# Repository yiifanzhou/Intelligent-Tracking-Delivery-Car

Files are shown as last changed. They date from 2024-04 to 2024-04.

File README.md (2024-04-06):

# Intelligent Tracking Delivery Car
This is a course design from Design &amp; Bulid Ⅰ(First Semester).  

<p align="center">
摘要
</p>  

&emsp;&emsp;为增加和改进现有轮式机器人功能，并为物流运输业提供更加智能化的选择，项目组致力于研发一种基于Arduino系统的能够自动循迹并精确投放的智能派送车。  

&emsp;&emsp;项目开发初期，通过资料收集、问卷调查、项目规划五步法、产品概念生成和选择的一般方法等研究方法，确定零件功能和市场需求、建立目标产品规格、分析并选择产品概念。中期，使用Solid works对零件进行三维建模以及组装；设计控制系统接线图和控制流程图；采用Arduino编程进行算法的设计和调试。后期，利用激光切割技术处理底板，采用3D打印技术打印投放装置，完成智能派送车实体模型的建立。

&emsp;&emsp;设计出的智能派送车能够自动沿黑线行进，并在多个投递处准确投放包裹，完成循迹与投放任务。

&emsp;&emsp;接下来是一些项目图片展示：  

</p>  

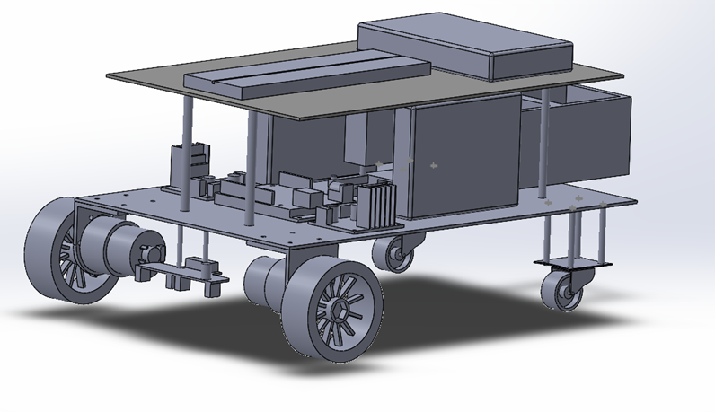
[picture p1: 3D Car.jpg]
  

<p align="center">
图1 整车设计图
</p>  

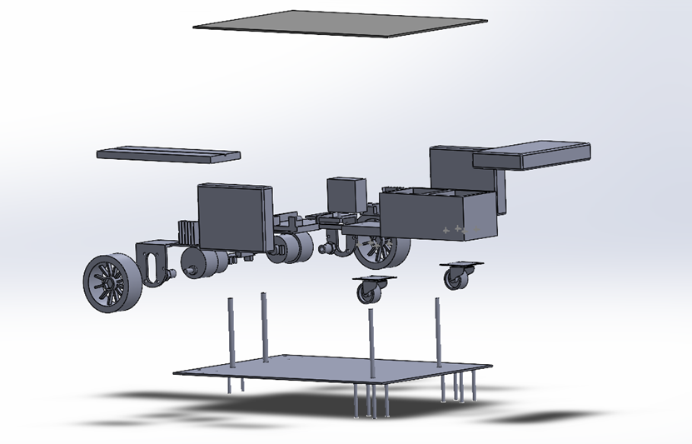
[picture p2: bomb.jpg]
   

<p align="center">
图2 整车爆炸图
</p>  

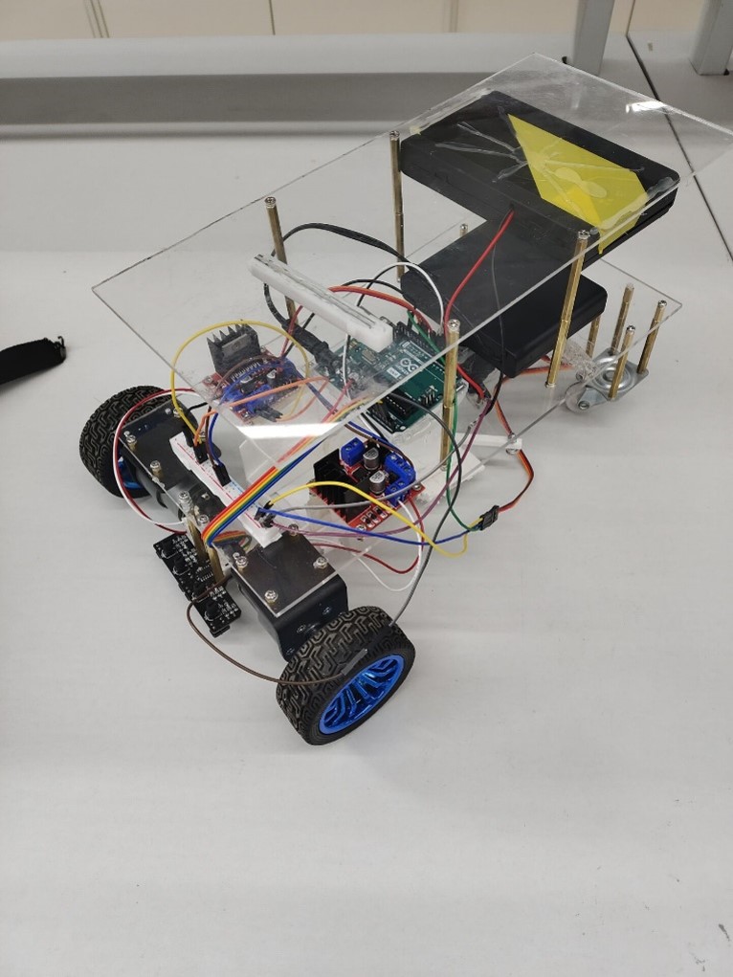
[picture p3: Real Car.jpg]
  

<p align="center">
图3 实物演示图
</p>

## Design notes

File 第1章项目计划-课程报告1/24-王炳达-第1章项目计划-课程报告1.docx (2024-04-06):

# 课程报告1 项目计划

## 1.1 项目相关资料综述

### 1.1.1 前言

随着科技的发展，智能派送车在各个领域都有广泛的应用前景，它可以代替人类完成恶劣环境下的货物搬运、设备检测等任务[1]。智能派送车是轮式移动机器人研究领域的一项重要内容，涵盖了机械、汽车电子、电气、计算机、检测技术、模式识别与智能控制等多个学科。它是陆地自主行驶车辆 (Autonomous Ground Vehicle) 的一种。AGV在社会生活的各个领域都有着非常广阔的应用前景。在西方发达国家，移动式自主服务机器人已广泛应用于医疗福利服务、商场超市服务、家庭服务等领域；AGV在军事领域也有着重要的应用价值， 美国军方把部分机器人技术视为未来战斗系统 (Future Combat System) 的重要组成部分[2]。本文基于基础的智能派送车展开资料查阅，对此进行研究。

### 1.1.2 智能小车的国内外研究现状

在国外，有关移动机器人的研究相对比较成熟。原因有二：一是研究起步早，二是投入经费多。上世纪50年代初，国外就开始对人工智能、机器人视觉、自动导航等技术进行理论层面的研究。进入上世纪90年代，移动机器人开拓各个应用领域，美国“火星探路者”、火星漫游车“索杰纳”、“勇气”号、“机遇”号相继进行探索，并完成科学探测任务。

在国内，对移动机器人的研究起步晚，研究的突破性进展比较少。国内最早从事智能汽车和智能交通研究的是清华大学，研究方向集中在汽车导航、车载微机、自主避障、行驶安全等方面。近年来，各个高校重点开展了移动机器人相关的研究，并获得一定成绩，如上海交通大学研制的高性能自主移动机器人Frontier-ITM，获得过国家863高技术计划专项支持。

### 1.1.3 项目产品组成

（1）直流减速电动机

直流减速电机是在直流电机（马达）的基础上配备了齿轮减速箱，从而能够提供较低的转速，及较大的力矩。其精度高、体积小、噪音低、耐用、耗能低、安装方便，适合本项目中对智能派送车的传动。

（2）传感器系统

传感器是一种检测装置，能感受到被测量的信息，并能将感受到的信息，按一定规律变换成为电信号或其他所需形式的信息输出，以满足信息的传输、处理、存储、显示、记录和控制等要求[3]。

项目组使用的是光学（红外）传感器，红外发射管不断发出红光，由于路线中地面与轨迹的颜色差异，使得接受管接收到的光强也有差异进，进而由转换元件输出特定的电流或电压信号，从而实现智能派送车的循迹功能。

（3）Arduino编程

Arduino并不仅仅是一块小小的电路板，还是一个开放的电子开发平台。它既包含了硬件——电路板，也包含了软件——开发环境和许许多多开发者、使用者创造的代码、程序。Arduino抛开了传统硬件开发的复杂操作，不需要了解硬件的内部结构和寄存器设置，也不需要过多的电子知识和编程知识，而只需通过简单的学习，了解各个引脚和函数的作用，便可利用它开发出各种出色的项目。

Arduino它的优势十分明显：一是跨平台，Arduino IDE可以在Windows、Mac OS X和Linux三大主流操作系统上运行，而其他的大多数控制器只能在Windows上开发；二是简单清晰的开发，Arduino IDE基于Processing IDE开发，这对于初学者来说极易掌握，同时又有着足够的灵活性，Arduino 语言是基于Wiring语言开发的，是对AVRGCC库的二次封装，并不需要太多的单片机基础和编程基础，只要简单地学习后就可以快速地进行开发；三是开放性，Arduino的硬件原理图、电路图、IDE软件及核心库文件都是开源的，在开源协议范围内可以任意修改原始设计及相应代码；四是从硬件开发趋势来说，Arduino不仅仅是全球最流行的开源硬件，也是一个优秀的硬件开发平台，更是硬件开发的趋势。

Arduino 简单的开发方式使得开发者更关注于创意与实现，可以更快地完成自己的项目开发，大大节约学习的成本，缩短开发的周期。鉴于Arduino的种种优势，越来越多的专业硬件开发者已经或开始使用Arduino来开发项目和产品；越来越多的软件开发者使用Arduino进人硬件、物联网等开发领域；在大学里，自动化、软件专业，甚至艺术专业，也纷纷开设了Arduino相关课程[4]。

（4）Solid works建模

Solid works是项目组在项目中对工件建模所采用的技术。Solid works软件功能强大，组件繁多，操作简单方便、易学易用。Solid works资源管理器是同Windows资源管理器一样的CAD文件管理器，用它可以方便地管理CAD文件。在强大的设计功能和易学易用的操作（包括Windows风格的拖/放、点/击、剪切/粘贴）协同下，项目组能在比较短的时间内完成更多智能派送车工件的设计，并更快地将高质量的产品投入后续打印工序。

（5）3D打印技术

3D打印技术即快速成型技术的一种，是一种以数字模型文件为基础，运用粉末状金属或塑料等可粘合材料，通过逐层打印的方式来构造物体的技术。项目中所使用的打印材料应具有较好的硬度、强度，以及一定的尺寸稳定性、耐磨性，且便于成型加工与机械加工。从而制作出较好的组件，继而进行组装工作。

## 1.2 项目管理

### 1.2.1 项目组成员

组长：王炳达；

组员：王宗辉、刘洋、周艺梵、郭法。

### 1.2.2 项目分工图

对智能派送车的各个模块进行划分，再分配给每位组员。工作分解结构图如图1-1所示。

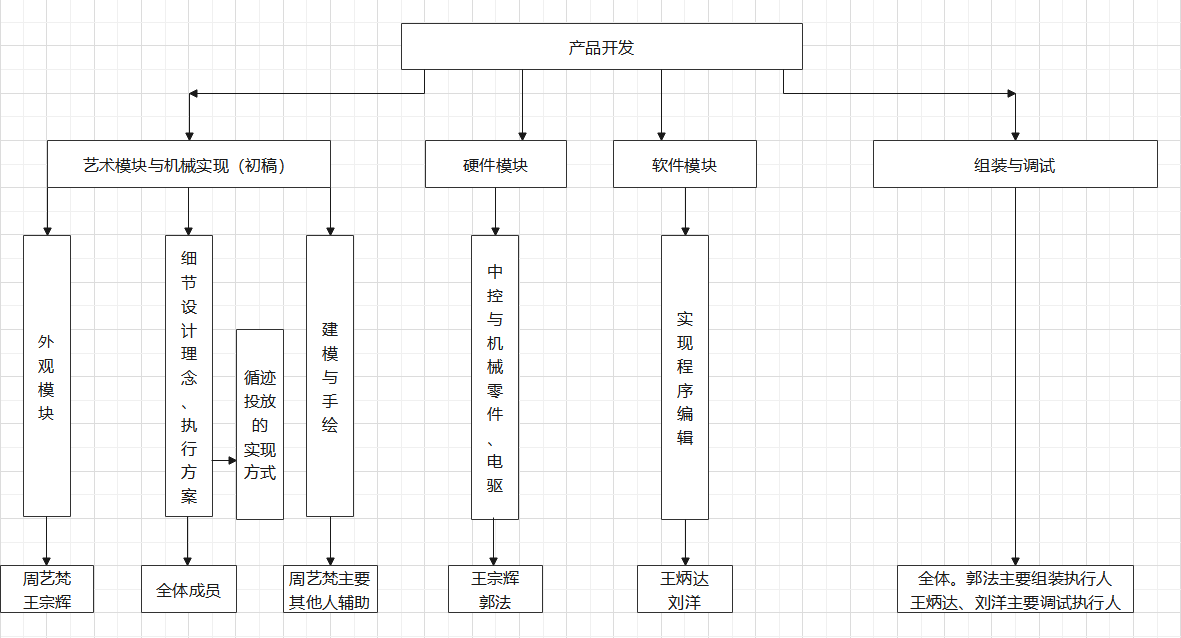
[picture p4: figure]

图1-1 工作分解结构图

### 1.2.3 进度安排甘特图

根据工作分解安排工作进度，进度安排甘特图如图1-2所示。

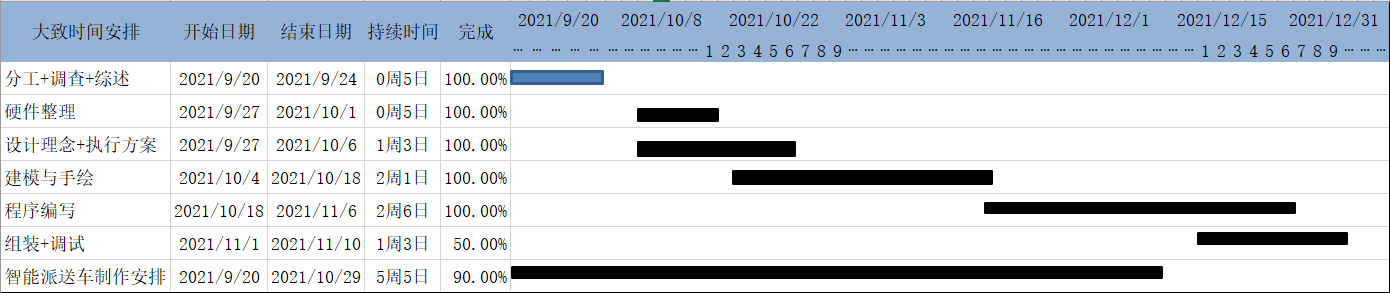
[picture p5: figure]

图1-2 进度安排甘特图

## 1.3 工程师职责

世界工程组织联盟提出了工程师伦理责任准则大致包括以下内容：

（1）应维护大众之安全、健康和福祉，以加强安全和环境的保护为最高指导原则。

（2）对技术后果负有责任，并且要告知公众技术可能的结果。

（3）严守业务机密，避免利益冲突。

（4）承办工程业务应以自己的专业领域提出服务与建议，态度应谨慎、认真。

（5）对待各方应持有公平、有礼、善意的态度，对雇主否决或忽视的重要工程的决策，应将可能发生的后果据理说明。

（6）吸收新的知识以加强专业能力。

（7）对他人违法或者有失伦理道德的一切工程技术上的决定或行为适时揭发。

根据上述条例对工程师不同层面的要求，现将其进行分类，如图1-3所示。

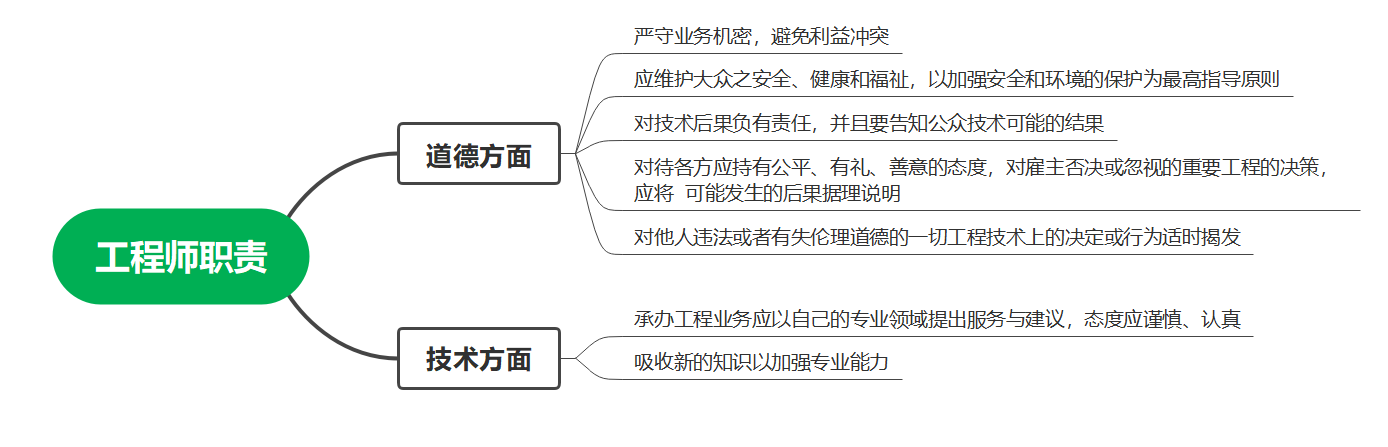
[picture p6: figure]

图1-3 工程师职责图

## 1.4 任务完成情况小结

在第5周至第8周期间，项目组对智能派送车的发展历程，现阶段所面临的一些问题以及应用前景进行初步的了解，并制定较为详细的制作计划。王炳达组织进行小组分工，并完成进度安排甘特图以及团队日历的制作；刘洋完成对工程师的职责的查找和分类；周艺梵完成课程报告PPT的制作；王宗辉完成项目相关资料的综述；郭法完成会议记录。

## 1.5 小组会议记录

“设计与建造”课程小组会议记录

议题 | “智能派送车”的初步规划与任务分工
组长 | 王炳达 | 年级/班级/组别 | | 2021级二班第4组
组员 | 郭法、周艺梵、王宗辉、刘洋
会议时间 | 2021年9月14日 19：00-21：00 | | 会议地点 | 郑东图书馆205读者研究厢
讨论内容 | 1．产品开发任务模块，进度。分为硬件，软件和组装等模块。 2．成员分工，工作分解。软件模块由王炳达负责；外观模块由周艺梵负责；细节设计理念由全体成员负责；建模与手绘主要由周艺梵负责；组装和调试主要由郭法负责。 3．PPT、文献综述、查阅资料的安排。PPT主要由周艺梵负责；文献综述由王宗辉和周艺梵负责；查阅资料硬件系统和结构模块由王宗辉负责，软件模块由周艺梵负责，工程师职责由刘洋负责。 4．各成员的相关问题和解决方案。讨论职责的细分和需要的资料和软件等事宜，都一一解决。 5．甘特图和日历的相关问题。规划将来任务并由王炳达做处理制作和完善。 6．PPT展示分工。王炳达负责讲分工和时间安排；王宗辉等三人负责讲相关资料；郭法负责讲会议记录。 7．智能派送车构造和软件使用相关情况。讨论关于智能派送车构件和材料，统一solid works的安装等事宜。
下一步工作计划 | 1．查阅资料以及个人综述，在各成员完成任务后。 2．讨论课程报告与PPT制作，在制作完成后统一讨论。 3．进一步讨论智能派送车的构造与硬件，在课程报告和PPT完成后。 4．讨论软件相关问题，下一次会议时间。
附件材料清单 | 无

参会成员：王炳达 刘洋 郭法 王宗辉 周艺梵

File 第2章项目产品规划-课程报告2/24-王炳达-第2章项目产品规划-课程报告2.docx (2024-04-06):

# 课程报告2 项目产品规划

## 2.1 项目产品规划

### 2.1.1 产品功能

项目组结合无人驾驶和无人派送货物的时代热点，在智能方面深度挖掘和深刻研究，设计出的智能派送车具备无人驾驶、自主自动循迹、定点准确投放包裹的功能，能够广泛应用于市场，充分满足人们需求，为智能派送这一方向提供建设性思路。

### 2.1.2 产品规划

（1）识别机会

在当今时代，网购等商业活动十分发达，但在这样一个智能化的时代，项目组发现重复性体力劳动给生活带来许多不便。经过讨论认为，智能派送车的出现，能够帮助人们减少体力劳动，具有广阔的潜在市场。同时，这样的产品也具有可行性，通过传感器系统、软件系统、硬件系统等各个系统的协同工作，达到智能派送的效果，同时也能够不断地迭代更新，升级产品。该产品具有较强的实用性，具有较好的获取市场份额的能力。通过项目组的不断分工和完善，该产品也能够具有较强竞争优势。更为关键的是，该产品投入成本小，风险小，值得尝试。

（2）评估并确定项目的优先级

项目组确保以客户为中心，确保满足客户的需求。同时，项目组也应当不断探索新的技术，争取在软硬件方面能够实现技术突破，实现技术方面的领先。

（3）分配资源和计划时间

任务分配和时间安排具体如上文中图1-1和1-2所示。

（4）完成项目前期规划

1）关键商业目标

① 支持小组战略目标：制作高效智能派送车。

② 产品推出时间：2022年1月14日前。

2）获益提议

① 产品性价比相对较高。

② 产品安全，不容易产生安全方面的问题。

③ 产品功能比较实用，节省人力。

3）主要市场

快递投放领域（公司为主）。

4）假设和约束

假设：

① 利用Solid works软件制图，进行建模与手绘。

② 掌握Arduino的编程知识。

③ 掌握中控与机械零件、电机驱动模块。

④ 实现组装和调试。

约束：

① 时间方面：可能会出现时间分配不当，进度缓慢的情况，项目组应按照甘特图进行适当改变。

② 经费方面：经费有限，需要合理利用各种分配的材料，做到效率最大化。

③ 能力方面：第一次接触软硬件知识，项目组应该努力学习相关方面的知识。

为更加直观地明确假设和约束内容，将假设和约束制成图表形式如下图2-1所示。

假设和约束
假设
利用Solid works进行制图，进行建模与手绘
掌握Arduino及其编程知识
约束
能力方面
掌握中控与机械零件、电机驱动模块
实现组装和调试
时间方面
经费方面

图2-1 假设和约束概念表

5）利益相关者

① 产品开发者：产品开发者通过制作开发掌握知识并学习技能。

② 产品使用者（个体）：减少不必要体力劳动，能够提高工作效率。

③ 快递公司：减少人力成本和财力成本，提高快递公司的利润。

④ 快递员：影响快递员的工作，在一定程度上减少快递员数量。

（5）反思过程和结果

1）经过项目组讨论，前期时间安排等工作存在不妥，项目组将灵活变更和调整完成产品的时间。

2）项目组未考虑使用创新的软硬件，应在这方面不断调整。

3）开发团队在时间管理方面存在部分问题，应提高工作效率。

## 2.2 客户需求调研

### 2.2.1 客户需求分析过程

（1）步骤一：收集来自客户的原始数据

通过调查问卷得到的客户需求数据如表2-1所示。

表2-1 智能派送车客户需求数据（客户调查表）

问题 | 客户需求 | 需求解释
智能派送车的安全性和可用性的评价与建议 | 如图2-2所示。 | 客户普遍认为安全性是可靠的。
智能派送车的产业化需要考虑的问题 | 如图2-3所示。 | 客户普遍认为要考虑安全性、人性化、环境识别度、成本以及接受度问题。
智能派送车的大范围推广和使用存在的阻碍 | 如图2-4所示。 | 客户认为大众可能会有心理接受上的障碍以及对安全的担心和成本的担忧。
市场上正在使用的智能派送车的改进点 | 如图2-5所示。 | 智能派送车的智能性和灵活度有待提高。
关于智能派送车的其他建议 | 希望得到更快的普及。 | 客户对智能派送车的未来抱有很高的期待。

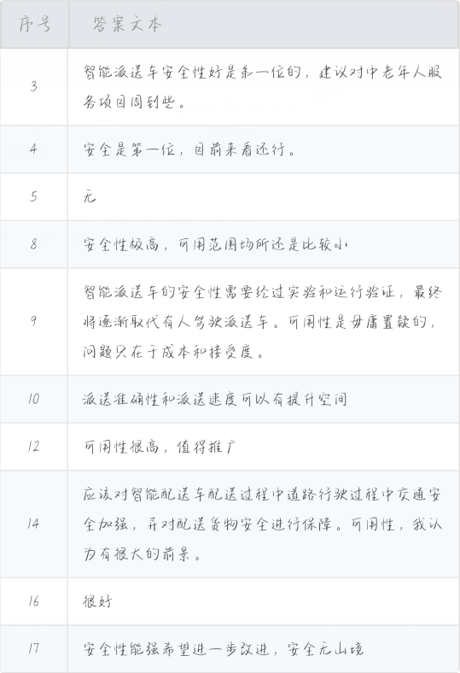
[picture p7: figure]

图2-2 智能派送车的安全性和可用性的评价与建议

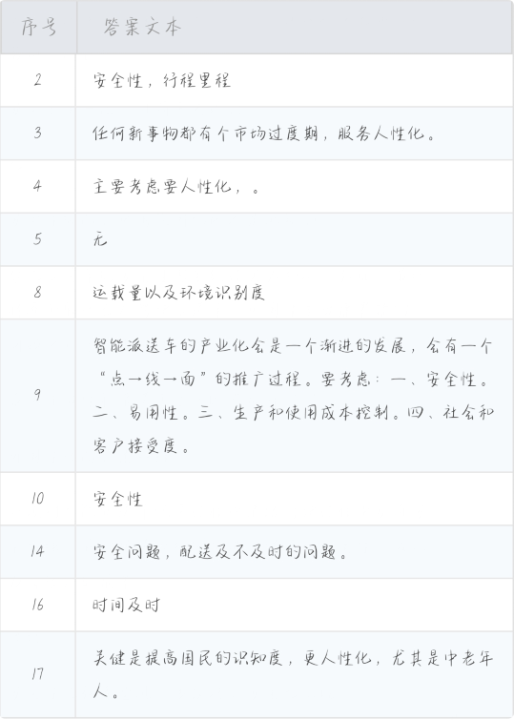
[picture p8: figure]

图2-3 智能派送车的产业化需要考虑的问题

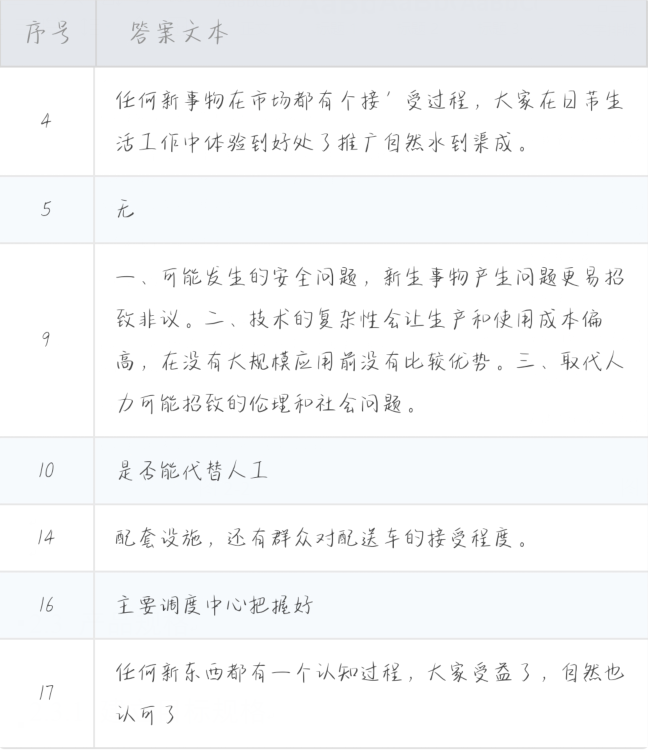
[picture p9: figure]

图2-4 智能派送车的大范围推广和使用存在的障碍

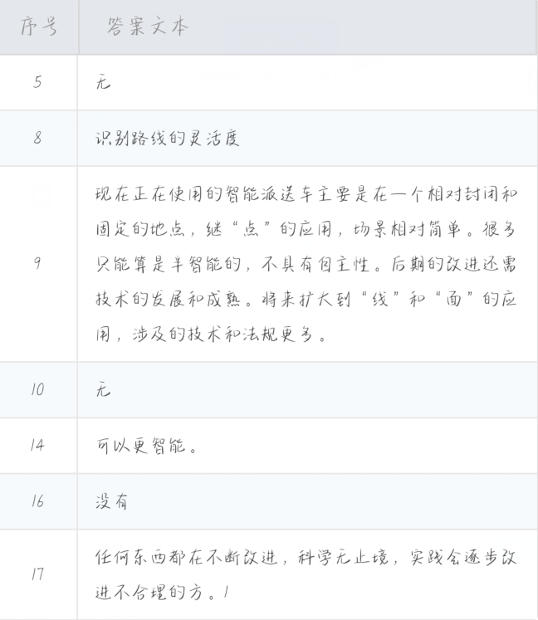
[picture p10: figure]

图2-5 市场上正在使用的智能派送车的改进点

（2）步骤二：根据客户需求解释原始数据

1）编写需求书的五个原则

① “做什么”而非“怎么做”。

② 产品特点。

③ 肯定而非否定。

④ 产品属性。

⑤ 避免“必须”和“应该”。

（3）步骤三：组织客户需求的层次结构

（4）步骤四：确定客户的需求的相对重要性

（5）步骤五：反思结果和过程

1）是否与目标市场上的主要顾客都进行了交流？

2）是否确定出已识别的最主要的需求？

3）是否捕捉到目标客户的潜在需求？

4）如何完善改进客户需求分析流程？

### 2.2.2 产品目标树

依据客户需求分级层次列表，可以绘制出产品目标树如图2-6所示，产品目标树显示客户需求的目标和子目标。

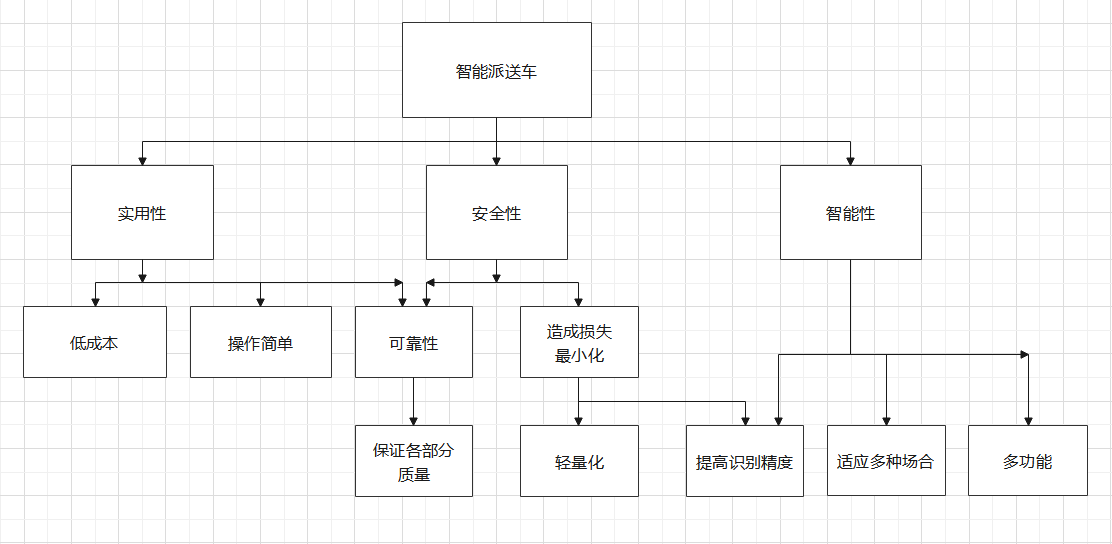
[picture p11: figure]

图2-6 产品目标树

## 2.3 产品规格

### 2.3.1 建立目标规格

（1）准备指标列表

为了在客户需求与度量指标之间建立联系，项目组需要了解用户的需求与智能派送车的性能，如表2-2所示。

表2-2 智能派送车需求列表

序号 | 需求
1 | 安全性
2 | 效率
3 | 派送费用
4 | 精准度

掌握所需指标可以准确设计出符合客户需求的智能派送车，智能派送车的指标列表如表2-3所示。

表2-3 智能派送车指标列表

序号 | 零件 | 单位 | 对应需求序号
1 | 车长 | mm | 1
2 | 车宽 | mm | 1
3 | 前轮直径 | mm | 2、4
4 | 转向轮直径 | mm | 4
5 | 物块大小 | mm*mm*mm | 2、3
6 | 物块存储器 | mm*mm*mm | 2、3
7 | 投放误差 | mm | 4
8 | 小车速度 | m/s | 2
9 | 电机电压 | V | 1、2
10 | 总价 | RMB | 3

（2）收集竞争产品的指标基准信息

通过调查资料了解竞争对手的详细规格信息，可以对项目组的智能派送车进行改进并更好满足客户的需求，竞争产品指标信息如表2-4所示。

表2-4 竞争产品指标信息

项目序号 | 项目 | 单位
1 | 前轮轮径、轮宽 | mm
2 | 转向轮轮径、轮宽 | mm
3 | 赛道测试时间 | s
4 | 传感器工作距离 | mm
5 | 车长、宽 | mm
6 | 电机电压 | V
7 | 小车车速 | m/s
8 | 总价 | RMB

（3）为每个指标设置理想值和临界可接受值

分析现有产品参数，为给定的产品指标设定目标值，包括理想值和临界可接受值，产品目标指标表如表2-5所示。

表2-5产品目标指标表

零件 | 目标值 | 理想值 | 临界可接受值
车长 | 250mm | 230-280mm | 200-300mm
车宽 | 150mm | 120-180mm | 100-200mm
前轮直径 | 60mm | 50-70mm | 40-70mm
转向轮直径 | 30mm | 25-35mm | 20-40mm
物块大小 | 50mm*50mm*50mm | 50mm*50mm*50mm
物块存储器 | 55mm*55mm*55mm | 60mm*60mm*60mm
投放误差 | 0 | 0-20mm | 0-40mm
电机电压 | 5V | 4.5-5.5V | 4-6V
总价 | 600RMB | 550-650RMB | 500-700RMB

（4）反思结果和过程

在确定产品指标中，项目组成员经过讨论与搜集资料，比对已有产品规格，衡量理想值，并为智能派送车做出合理临界值。

### 2.3.2 产品规格参数表

罗列材料清单，查询估计每一个组件的购买价格，初步预估产品成本。从成本角度进行估算能设计出更符合客户需求的产品，智能派送车的组件清单列表如表2-6所示。

表2-6 智能派送车的组件清单列表

组件名称 | 数量 | 参考单价/元
Arduino开发板 | 1套 | 150
面包板 | 2块 | 10
接插线 | 1套 | 20
电池盒 | 2个 | 10
直流减速电动机 | 2个 | 30
电动机驱动模块 | 2个 | 30
传感器模块 | 2个 | 50
3D打印材料 | 不限 | 350

### 2.3.3 需求——指标矩阵

使用需求指标矩阵可以更加明确地表示出客户需求与度量指标之间的联系，如表2-7所示。

表2-7 智能派送车的需求——指标矩阵

指标 需求 | | 1 | 2 | 3 | 4 | 5 | 6 | 7 | 8 | 9
| | 小车的宽度 | 优化软件功能 | 额定载重量 | 转弯半径 | 停位精度 | 投放精度 | 行驶速度 | 工作电压 | 传感器灵敏度
1 | 小车的安全性 | • | | | •
2 | 提高小车速度 | | | | | | | • | •
3 | 获知位置信息 | | | | | • | | | | •
4 | 保护用户隐私 | | • | | | | | | | •
5 | 降低派送费用 | | | •
6 | 提高额定载重量 | | | •
7 | 提升投放精准度 | | | | | | • | | | •
8 | 自动识路功能 | | | | | | | | | •

## 2.4 任务完成情况小结

在第9周至第11周期间，项目组对智能派送车的产品规划进行完善，面向社会大众进行客户需求调研，并制定较为详细的制作计划。王炳达对客户需求进行调查；刘洋完成产品的详细规划；周艺梵、郭法完成产品规格的明确；王宗辉对小组会议进行记录以及对任务完成情况进行总结。

## 2.5 小组会议记录

“设计与建造”课程小组会议记录

议题 | “智能循迹派送小车”的项目规划
组长 | 王炳达 | 年级/班级/组别 | | 2021级二班第4组
组员 | 郭法、周艺梵、王宗辉、刘洋
会议时间 | 2021年10月14日19：00-21：00 | | 会议地点 | 郑东图书馆406读者研究厢
讨论内容 | 1．项目规划包含产品规划五步骤和产品任务书。 2．成员分工，工作分解。客户需求调研由王炳达负责；PPT、产品规格由周艺梵、郭法负责；产品规划由刘洋负责；小组会议记录和任务完成小结有王宗辉负责。 3．各成员的相关问题和解决方案。讨论职责的细分和需要进行的问卷调查等事宜，都一一解决。 4．甘特图和日历的相关问题。规划将来任务并由王炳达做处理制作和完善。 5．小车规格应按照客户调查表明确目标、需求和指标。
下一步工作计划 | 1．在各成员完成任务后进行各成员工作的整合与细节讨论。 2．讨论课程报告与PPT制作，在制作完成后统一讨论。 3．在课程报告和PPT完成后进一步讨论派送小车的构造与硬件。 4．报告完成后，进行建模软件的使用训练与组员间互传文件的统一。
附件材料清单 | 无

参会成员：王炳达 刘洋 郭法 王宗辉 周艺梵

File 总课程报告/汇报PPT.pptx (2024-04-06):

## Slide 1

求是学部二班4组答辩

组长：王炳达

组员：王宗辉、周艺梵、郭法、刘洋

PLEASE ADD YOUR TITTLE HERE

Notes: 亮亮图文旗舰店https://liangliangtuwen.tmall.com

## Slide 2

摘要

为增加和改进现有轮式机器人功能，并为物流运输业提供更加智能化的选择，项目组致力于研发一种基于Arduino系统的能够自动循迹并精确投放的智能派送车。
项目开发初期，通过资料收集、问卷调查、项目规划五步法、产品概念生成和选择的一般方法等研究方法，确定零件功能和市场需求、建立目标产品规格、分析并选择产品概念。
中期，使用Solid works对零件进行三维建模以及组装；设计控制系统接线图和控制流程图；采用Arduino编程进行算法的设计和调试。
后期，利用激光切割技术处理底板，采用3D打印技术打印投放装置，完成智能派送车实体模型的建立。
设计出的智能派送车能够自动沿黑线行进，并在多个投递处准确投放包裹，完成循迹与投放任务。

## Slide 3

目录

CONTENTS

01

背景与意义

02

研究的重难点

03

实际中的问题和解决方案

总结

04

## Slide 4

背景与意义

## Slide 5

背景与意义

随着科技的发展，智能派送车在各个领域都有广泛的应用前景，它可以代替人类完成恶劣环境下的货物搬运、设备检测等任务[1]。智能派送车是轮式移动机器人研究领域的一项重要内容，涵盖了机械、汽车电子、电气、计算机、检测技术、模式识别与智能控制等多个学科。它是陆地自主行驶车辆 (Autonomous Ground Vehicle) 的一种。AGV在社会生活的各个领域都有着非常广阔的应用前景。在西方发达国家，移动式自主服务机器人已广泛应用于医疗福利服务、商场超市服务、家庭服务等领域；AGV在军事领域也有着重要的应用价值， 美国军方把部分机器人技术视为未来战斗系统 (Future Combat System) 的重要组成部分
通过本项目组对智能派送车的研究，可以实现智能派送车的循迹与投放，可以与各快递公司或者驿站进行合作进行初步的商业化，有效解决快递行业关于“最后一公里”的问题。

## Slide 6

背景与意义

收集来自客户的原始数据
通过调查问卷得到的客户需求数据如表所示。
智能派送车客户需求数据

问题 | 客户需求 | 需求解释
智能派送车的安全性和可用性的评价与建议 | 如图1所示。 | 客户普遍认为安全性是可靠的。
智能派送车的产业化需要考虑的问题 | 如图2所示。 | 客户普遍认为要考虑安全性、人性化、环境识别度、成本以及接受度问题。
智能派送车的大范围推广和使用存在的阻碍 | 如图3所示。 | 客户认为大众可能会有心理接受上的障碍以及对安全的担心和成本的担忧。
市场上正在使用的智能派送车的改进点 | 如图4所示。 | 智能派送车的智能性和灵活度有待提高。
关于智能派送车的其他建议 | 希望得到更快的普及。 | 客户对智能派送车的未来抱有很高的期待。

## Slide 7

背景与意义


图1 智能派送车的安全性和可用性的评价与建议


图2 智能派送车的产业化需要考虑的问题

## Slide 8

背景与意义


图3 智能派送车的大范围推广和使用存在的障碍


图4 市场上正在使用的智能派送车的改进点

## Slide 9

研究的重难点

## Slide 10

研究的重难点

投放装置

利用什么对物块进行投放？利用什么制作投放装置？
怎样实现投放精准？

循迹

有哪些方案可以实现小车的循迹
哪种方案最好？为什么？

Arduino编程

如何让传感器和Arduino之间建立联系？
小车转向的速度该控制为多少？

连线

线路如何连接才正确？
如何让线路变得不那么繁琐？

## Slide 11

研究的重难点——方案选择

经过小组讨论，小组最终决定使用差速转向和推杆式投放

转向：转向分为差速转向和舵机转向。
差速转向：即小车通过控制左右两个驱动轮的转速不同实现转向，当驱动轮转速不同时，即使无转向轮或者转向轮停止，车身也会旋转，但车辆转向的角度无法精确控制。
舵机转向：舵机转向能够精确控制转向角度，实现智能派送车准确循迹，但其耗电大且安装复杂。赛道类小车对精度的要求不高且差速转向更容易实现，因此，项目组采用差速转向方式。
投放：投放是智能派送车的重要功能，其方案多种多样，包括：自由落体式、机械臂式、传送带式、推杆式、推隔板式。
自由落体式投放成本低、开发简单、不需要维护。但投放误差大、包裹易损坏、工作效率低。
机械臂式投放位置精确、动作灵活、可操作性强，但搬运包裹时间长、效率低，设计过程和计算机模拟耗费时间长、技术难度大。
传送带运行平稳安全、噪音少、包裹投放具有一定的精度。但包裹传送和投放速度慢、效率低并且存在磨损打滑问题。推杆式投放精确度高、投放速度快、效率高，正常使用期间长期免维护，成本适中、开发周期短。但曲柄的往复运动可能会损坏其他零件且存在噪音。
推隔板式投放利用连杆推动包裹，包裹从洞中掉落，保障包裹分隔，不会出现多个包裹一起掉落情况，但仍然会造成包裹损坏等问题。综合投放精准度、投放速度、包裹安全性考虑，项目组决定采用推杆式投放。

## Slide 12

研究的重难点——功能分析

差速转向：智能派送车循迹时通过红外传感器识别两种情况，一是识别黑色行进线，二是识别黑色十字线。
当智能派送车行进时，左右红外传感器发出信号并接收来自路况反馈的信号。通过Arduino分析控制，左右均未检测到黑线，左右两轮速度相等，智能派送车直行；左边检测到黑线，右边未检测到黑线，左轮速度小于右轮速度，智能派送车左转；左边未检测到黑线，右边检测到黑线，左轮速度大于右轮速度，智能派送车右转，通过这三方面实现智能派送车的循迹功能。

当智能派送车识别到黑色十字线时，驱动电机停止运行，智能派送车由于有行进速度，因此做减速运动。通过Arduino分析控制，作用于推杆的电机运行，包裹准确投放至指定位置。随后作用于推杆的电机停止运行，驱动电机运行，智能派送车继续完成循迹功能与下一阶段的包裹投放。

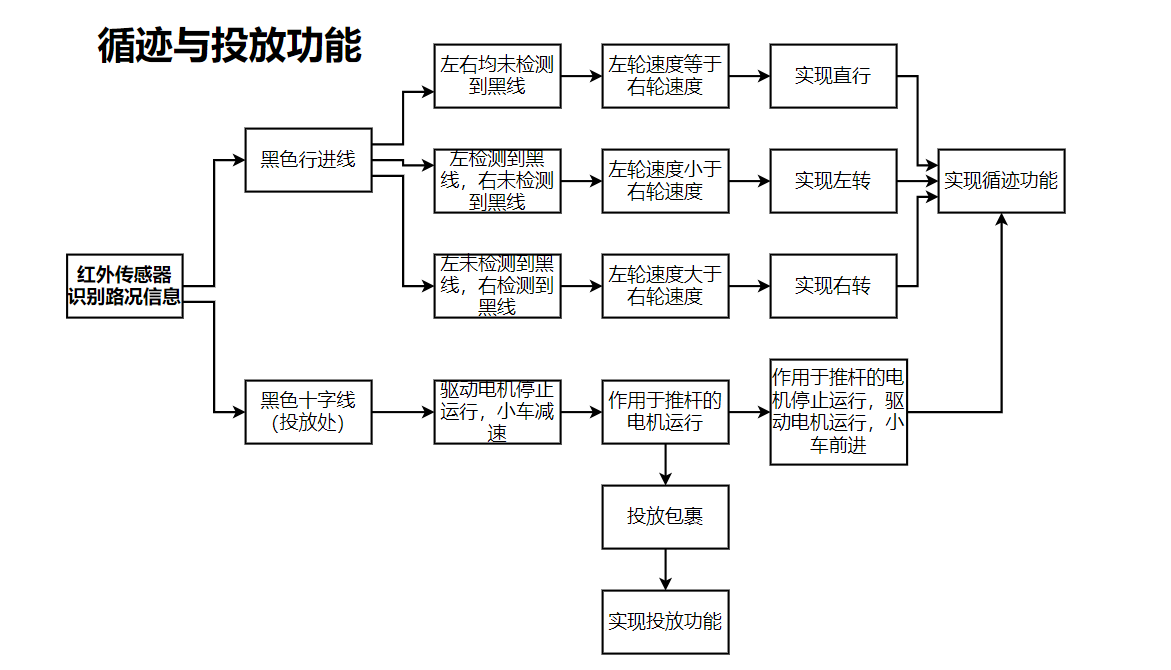
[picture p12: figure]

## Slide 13

研究的重难点——投放设计

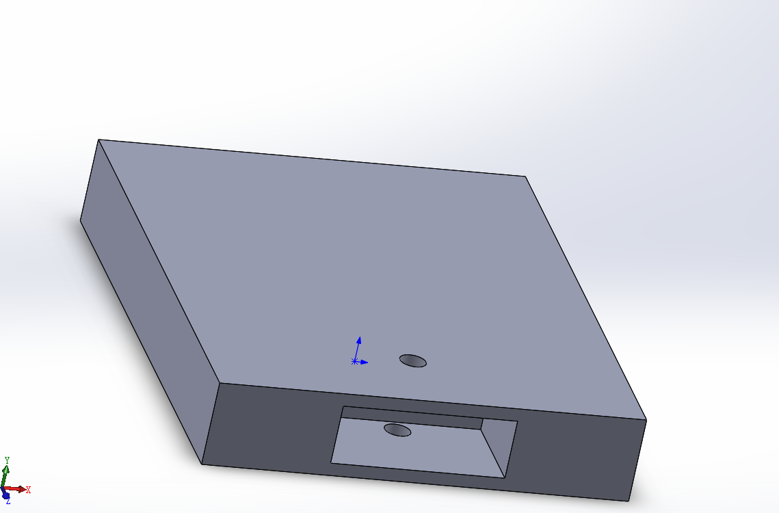
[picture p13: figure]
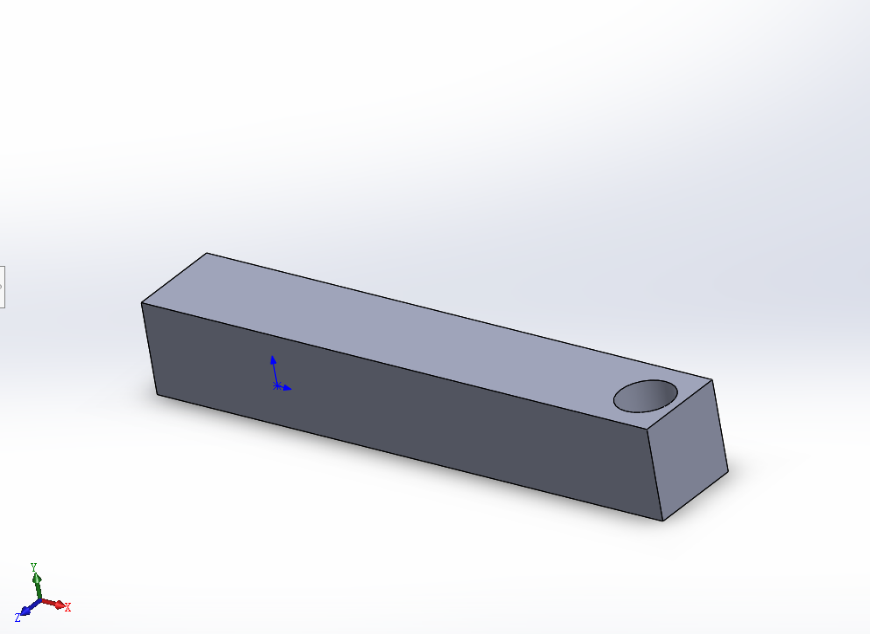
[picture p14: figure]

连杆1

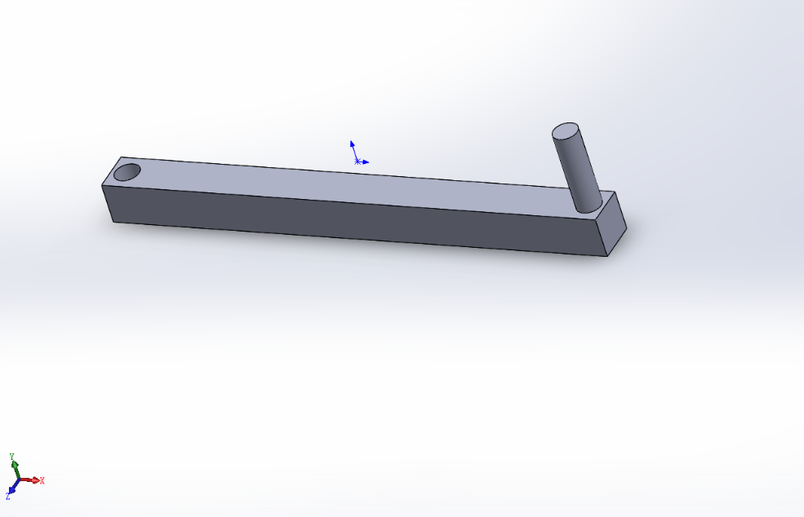
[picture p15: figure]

推块

连杆2

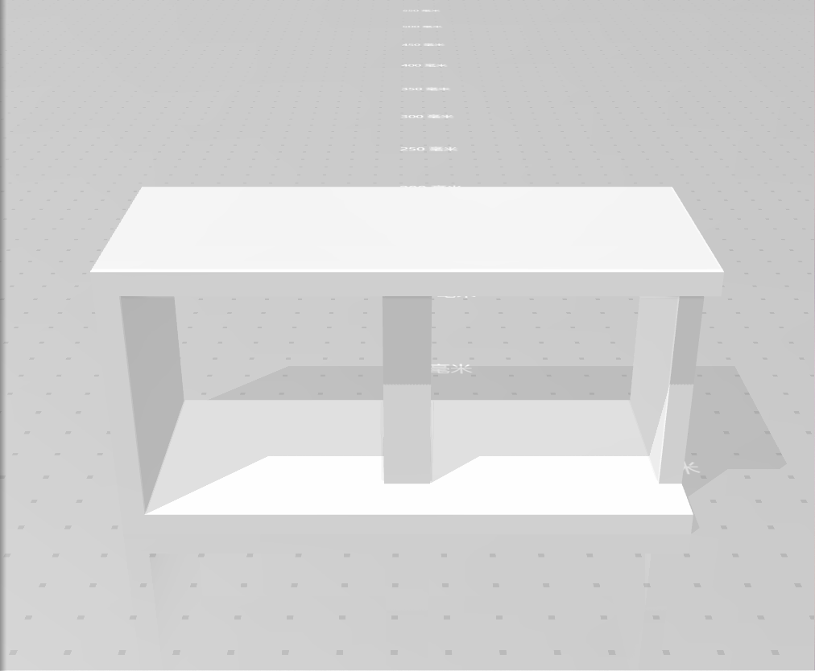
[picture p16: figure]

经过小组研究决定，利用舵机连接连杆，舵机的运动使得连杆转动，并使得推快移动推动物块，使得在最底层的物块从如左下图的载物盒里的推出，

载物盒

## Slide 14

研究的重难点——接线设计

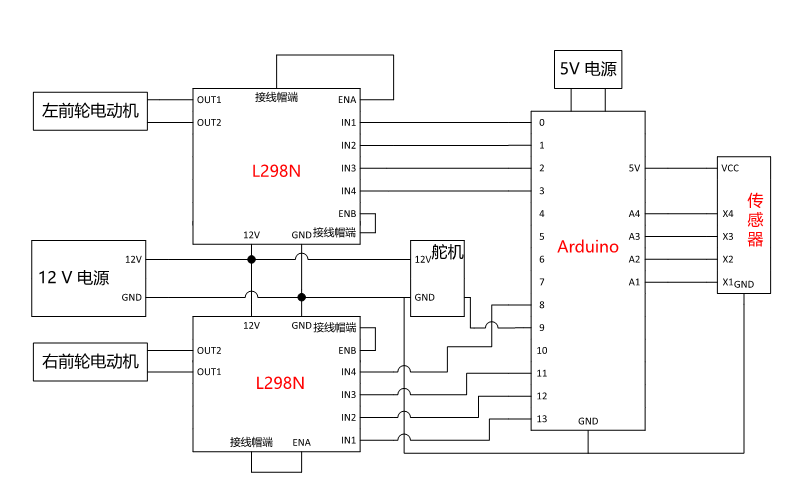
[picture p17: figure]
小车控制系统原理图
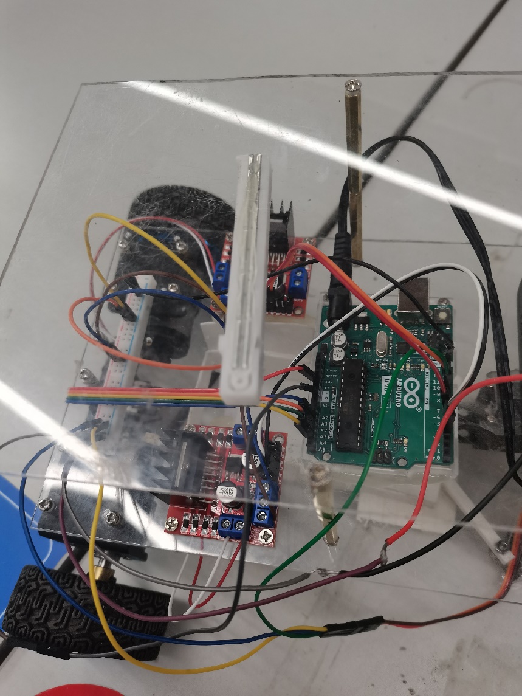
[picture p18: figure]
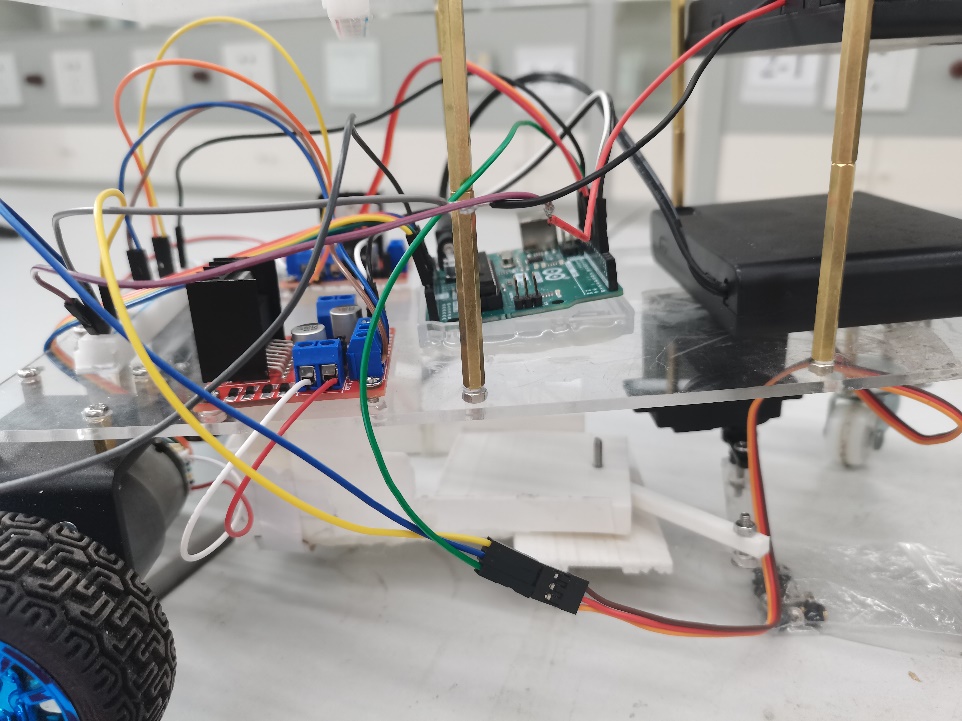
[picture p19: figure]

小组经过对各功能的分析，对小车线路连接如上图所示

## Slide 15

研究的重难点——总体结构设计

对于智能派送车整车结构设计，项目组采用双层结构、前轮驱动模式、差速转向机构、推杆式投放机构，如手绘概念图4-1所示。
双层结构能够保证小车的空间充裕和零件的摆放整齐，驱动前轮利用两轮的速度差转向，双万向后轮保证小车的稳定性，投放利用舵机控制推杆的转动将包裹推下，舵机可以控制精度保证包裹的准确落地。
智能派送车的第一层，红外传感器位于车的前部，从车底盘探出，便于精准识别黑线。两个小电池盒对立放置在两侧，维持小车平衡。电机驱动器对应放在两驱动前轮上方，Arduino开发板放置在两电机驱动器之间。第二层放置大电池盒和面包板，便于杜邦线的连接整理。
零部件之间的连接方式分为插孔式连接、螺栓螺母连接、铜柱连接。其中驱动轮与驱动电机，投放箱与下底板之间为插孔式连接。电机支架与电机、电机支架与下底板、电机驱动模块与下底板、面包板与上底板、Arduino开发板与下底板之间为螺栓螺母连接。上下底板之间、传感器与下底板、万向轮与下底板之间为铜柱连接。

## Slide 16

实际中的问题和解决方案

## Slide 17

实际中的问题和解决方案

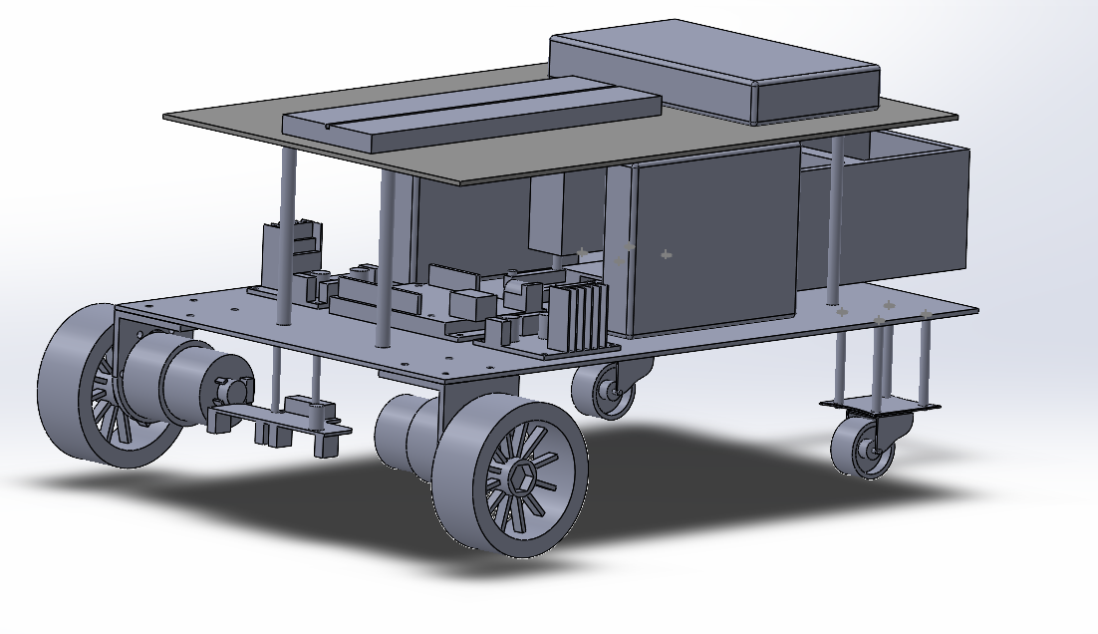
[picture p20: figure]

最终我们设计出的小车模型如左图所示。但是在实际操作中，发现投放装置如果在下底板上方，可能会导致投放精度不够，程序难以实现的问题，所以实际方案中，我们将投放装置置于下底板传感器后方，确保投放尽量精准。同时为了防止物块被置物盒卡住，通过在前后轮增加铜柱，我们整体提高了下底板的高度。

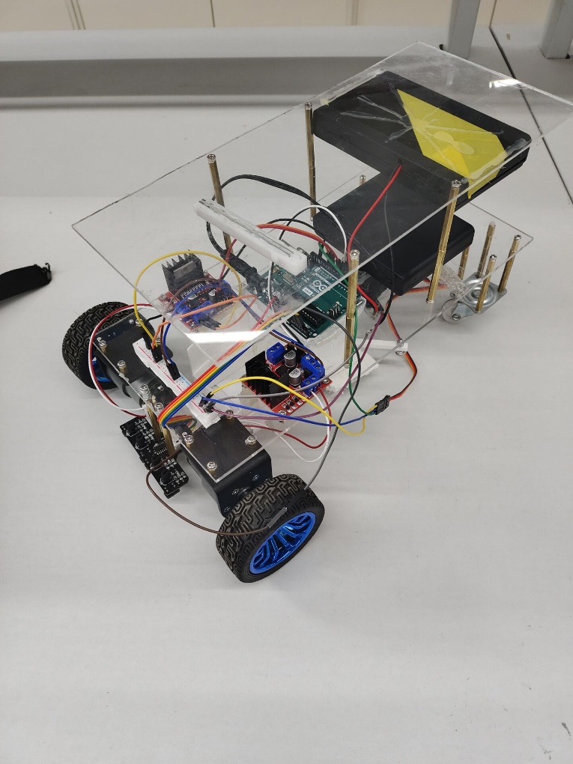
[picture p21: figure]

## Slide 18

实际中的问题和解决方案

在实际操作中，由于将置物盒改到下底板，所以置物盒又增加了一层底板，发现推块推动物块，可能会导致物块和底板接触，但并不下落的情况。如果减少底板面积，可以使物块更容易下落，但是又可能会导致之后的物块滑落。
所以，小组增加了如左图下方的连杆的长度，这样，能够增加小车推块的运动长度更长，确保能够推动物块到地面，同时保证第二个物块稳定地落到底板

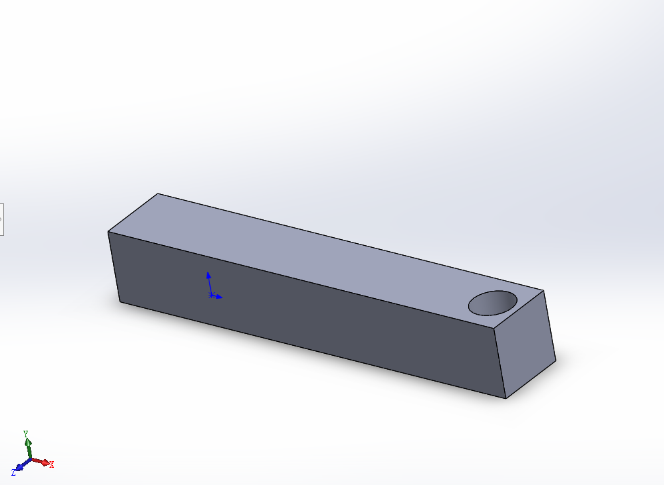
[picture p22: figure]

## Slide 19

实际中的问题和解决方案

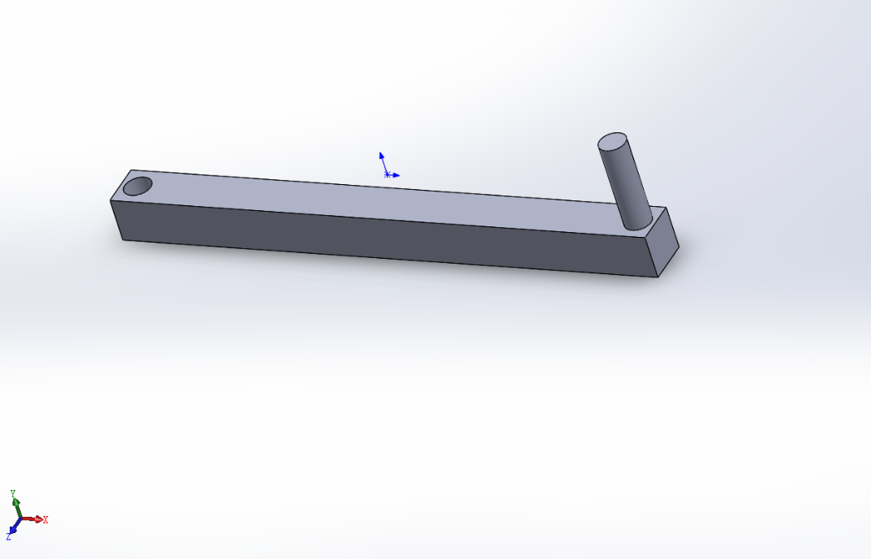
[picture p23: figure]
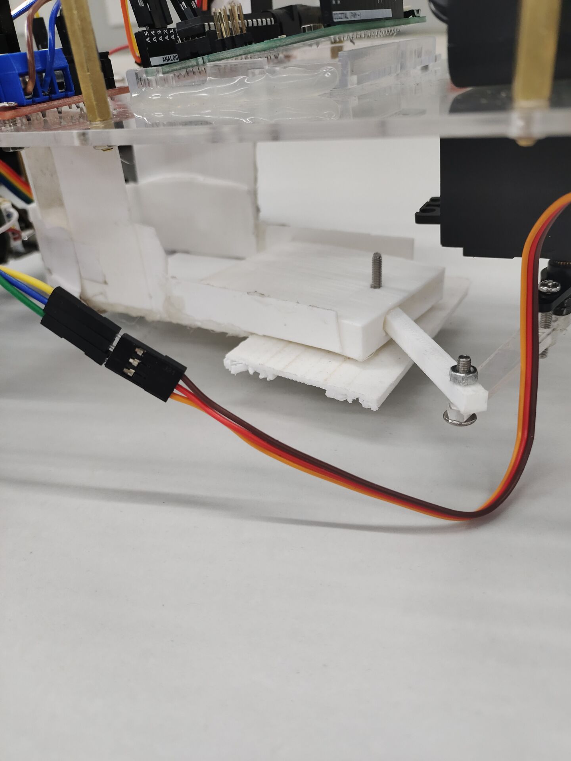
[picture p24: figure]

我们原计划3D打印如图左边的两个连杆，但是在实际操作中，3D打印的精度较差，无法实现两个连杆的连接。此外，由于两个连杆的尺寸较小，左上图的连杆上的小圆柱容易弯折损坏，于是在实际操作过程中，小组决定通过打孔来连接连杆。

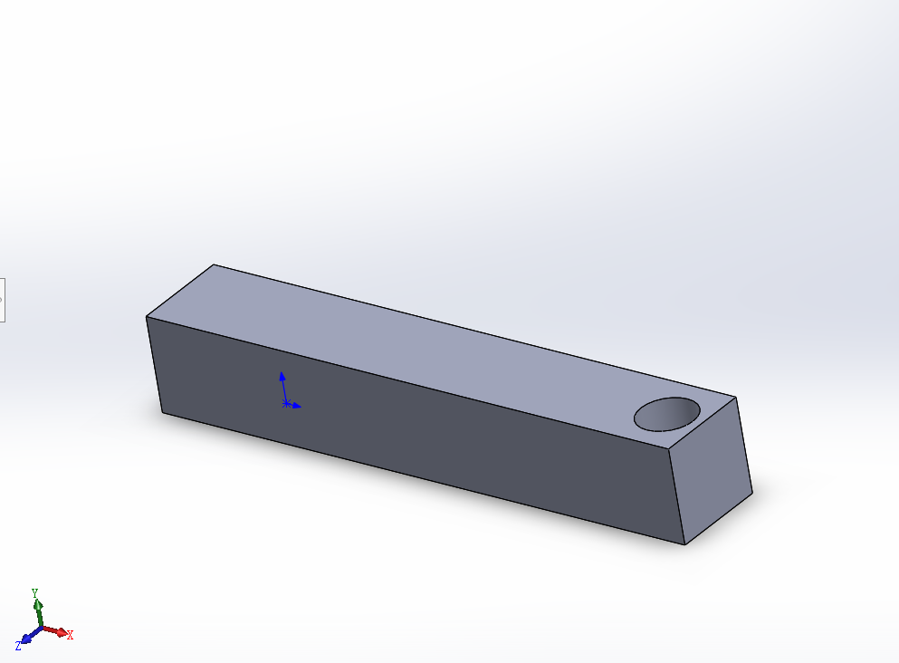
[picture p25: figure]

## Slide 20

实际中的问题和解决方案

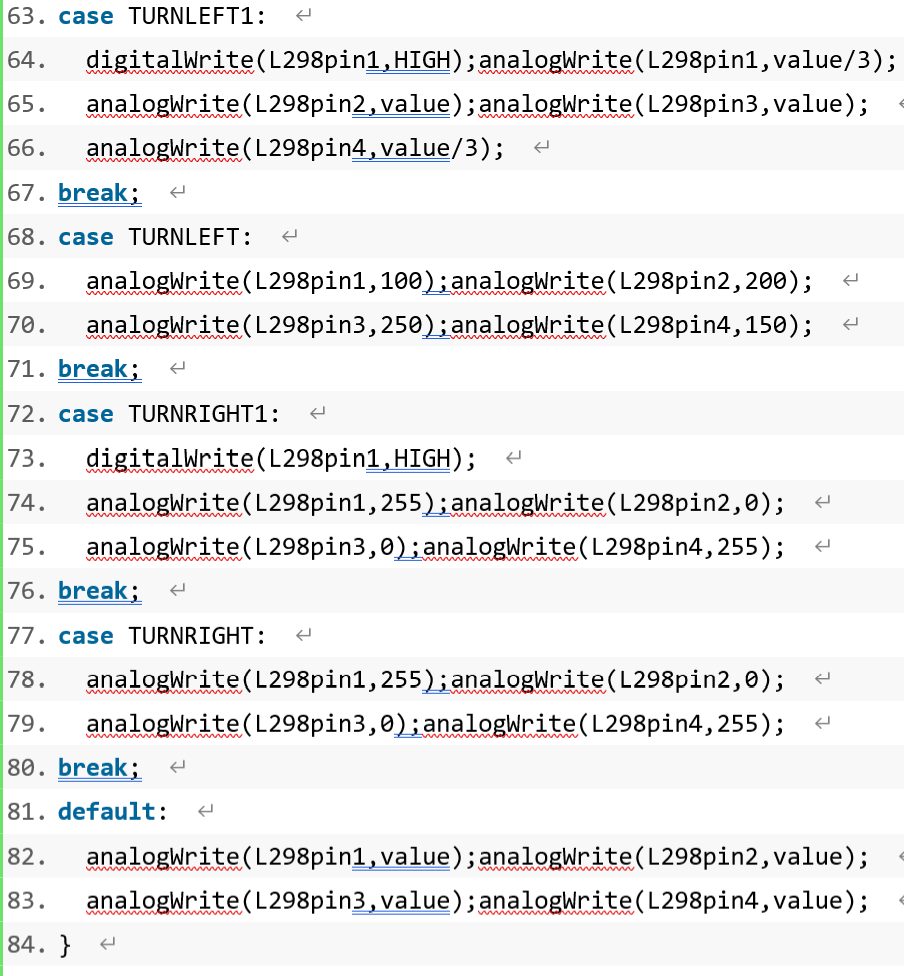
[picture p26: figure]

小组在设计小车转向时使用代码控制速度，但是由于小车结构的原因，小组组员多次改变小车代码中速度的值，避免小车转向时因速度过快而偏离轨道，避免小车在转向时打滑。

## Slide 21

实际中的问题和解决方案

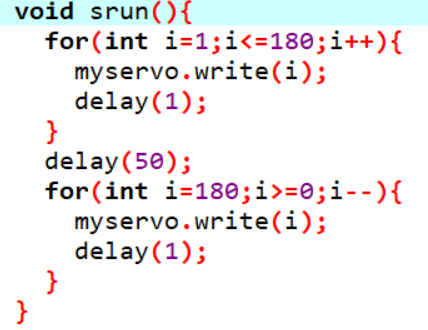
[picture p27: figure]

投放


循迹

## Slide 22

总结

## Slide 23

总结——社会影响

最后小组成功克服困难并设计出了满足循迹和投放功能的小车

总的来说，智能派送车进入市场将对快递和运输等行业带来革命性的影响：
（1）能够解放劳动力，有利于劳动力的转型升级。
（2）降低快递公司的派送成本，提高派送效率，有利于降低快递价格和提高快递公司经济收入。
（3）使快递运往一些地势复杂、经济落后的偏远地区更加便捷。
（4）若快速大范围应用，有可能造成一定的失业问题。

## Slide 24

总结——团队总结

对于求是学部二班4组的组员来说，大家团结协作，共同设计出了完成要求的智能派送小车，在这过程中：
（1）我们学习到了相关的专业知识，如3D建模，3D打印
（2）通过合作，我们培养了沟通协作能力
（3）拓宽了眼界，对各专业相关知识有了更深的了解，利于未来专业选择。
（4）通过对项目式课程的深入学习，了解了完成一个项目的基本流程，对完成项目的各项要求有了一定的了解
（5）培养了在面对困难时冷静分析解决问题的能力
（6）增进同学感情

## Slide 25

感谢老师们的辛勤付出！

感谢观看！

Thans for watching

求是二班四组

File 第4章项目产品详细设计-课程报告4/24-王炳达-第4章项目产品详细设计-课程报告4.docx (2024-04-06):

# 课程报告4 项目产品详细设计

## 4.1 项目产品结构设计

### 4.1.1 项目产品整车结构设计

对于智能派送车整车结构设计，项目组采用双层结构、前轮驱动模式、差速转向机构、推杆式投放机构，如手绘概念图4-1所示。

双层结构能够保证小车的空间充裕和零件的摆放整齐，驱动前轮利用两轮的速度差转向，双万向后轮保证小车的稳定性，投放利用舵机控制推杆的转动将包裹推下，舵机可以控制精度保证包裹的准确落地。

智能派送车的第一层，红外传感器位于车的前部，从车底盘探出，便于精准识别黑线。两个小电池盒对立放置在两侧，维持小车平衡。电机驱动器对应放在两驱动前轮上方，Arduino开发板放置在两电机驱动器之间。第二层放置大电池盒和面包板，便于杜邦线的连接整理。

零部件之间的连接方式分为插孔式连接、螺栓螺母连接、铜柱连接。其中驱动轮与驱动电机，投放箱与下底板之间为插孔式连接。电机支架与电机、电机支架与下底板、电机驱动模块与下底板、面包板与上底板、Arduino开发板与下底板之间为螺栓螺母连接。上下底板之间、传感器与下底板、万向轮与下底板之间为铜柱连接。


图4-1 手绘概念草图

### 4.1.2 标准件及配件选用

项目组清点并核实智能派送车的标准件及配件，包括：电池盒、驱动轮、万向轮、电机、电机驱动器、面包板、Arduino开发板、四路红外传感器以及若干铜柱。各个零件的具体数目和信息，如表4-1所示。

表4-1 标准件及配件清单

标准件及配件 | 数目 | 备注
电池盒 | 3 | 大电池盒2个，小电池盒1个
电机驱动器 | 2 | 选用L298N电机驱动模块
万向轮 | 2
驱动轮 | 2
电机 | 3 | 两种不同型号的减速电机
面包板 | 1
传感器 | 1 | 四路红外传感器
铜柱 | 若干 | 含多种型号
Arduino开发板 | 1

### 4.1.3 转向机构设计

智能派送车的转向机构包含在驱动机构中，如图4-2所示。驱动机构由电机、电机支架、电机驱动模块和驱动轮构成，电机驱动模块控制电机，在传感器感知压线信号后，电机提供不同转速，利用两驱动前轮的差速及万向后轮的配合进行急转或者缓转。


图4-2 智能派送车转向机构设计

### 4.1.4 投放机构设计

智能派送车的投放机构由电机、储存盒和投放盒构成，如图4-3所示。下图中，左侧盒子为投放盒，投放盒放置在底板外并挖出空格，便于包裹掉落；右侧盒子为储存盒，放置在底板上，用于储存包裹。电机转动一周，由横杆推动包裹向前，使包裹掉落，实现包裹的单次投放，之后循环这一过程完成所有投放任务。


图4-3 智能派送车投放机构设计

## 4.2 建立项目产品3D模型

### 4.2.1 智能派送车3D视图

项目组通过Solid works软件将智能派送车的各个零件进行装配，按照智能派送车整车结构设计放置各个零件，得到智能派送车的3D视图，如图4-4所示。


图4-4 智能派送车3D视图

### 4.2.2 智能派送车爆炸图

为方便查看装配体中各零件之间的装配关系以及各个零件的装配过程，项目组制作智能派送车爆炸图，如图4-5所示。在爆炸图中，零件按照装配关系偏离原来的装配位置，将复杂的小车结构清晰地呈现出来。


图4-5 智能派送车爆炸图

## 4.3 绘制项目产品3D图和2D图

项目组成员对各个零件的结构和功能进行分析，绘制各个零件的3D图和2D图，清楚表达小车的具体细节。

（1）Arduino开发板：作为总控制系统，其可接收红外传感器信号、识别黑线信号以及控制驱动和投放装置。其3D图和2D图如图4-6和图4-7所示。


图4-6 Arduino开发板3D图

图4-7 Arduino开发板2D图

（2）四路红外传感器：红外传感器电路设计相对简单，检测信息速度快且成本低。检测四个位置的路况信息，确定小车的循迹情况，能够较精准地确定小车相对轨迹黑线的位置，并保证小车能感知投放定位点，从而发出刹车命令。 其3D图和2D图如图4-8和图4-9所示。


图4-8 四路红外传感器3D图


图4-9 四路红外传感器2D图

（3）电机：产生驱动转矩，作为动力源将电源的电能转化为机械能，通过传动装置或直接驱动车轮进行转动。其3D图和2D图如图4-10和图4-11所示。


图4-10 电机3D图


图4-11 电机2D图

（4）电机联轴器：联轴器将电机与旋转轴连接，通过旋转轴传递动力。其3D图和2D图如图4-12和图4-13所示。


图4-12 电机联轴器3D图


图4-13 电机联轴器2D图

（6）电机板：固定电机与底板。其3D图和2D图如图4-14和图4-15所示。


图4-14 电机板3D图


图4-15 电机板2D图

（7）舵机：舵机是一种角度伺服的驱动，可以精准控制角度实现投放包裹的准确。其3D图和2D图如图4-16和图4-17所示。


图4-16 舵机3D图


图4-17 舵机2D图

（8）面包板：面包板上存在很多小插孔，可以省略焊接步骤，节省电路的组装时间，对于项目组智能派送车的电路连接十分重要。其3D图和2D图如图4-18和图4-19所示。


图4-18 面包板3D图


图4-19 面包板2D图

（9）驱动轮：实现小车的循迹功能，并通过两轮的配合实现转向。其3D图和2D图如图4-20和图4-21所示。

图4-20 驱动轮3D图


图4-21 驱动轮2D图

（10）万向轮：使小车后轮能够灵活地跟随前轮转弯，保证小车沿轨迹正常行进。其3D图和2D图如图4-22和图4-23所示。


图4-22 万向轮3D图


图4-23 万向轮2D图

（11）电池盒：储存作为电源的电池，将电池与外部零件分隔开，便于更好地提供电能。其3D图和2D图如图4-24和图4-25所示。


图4-24 电池盒3D图


图4-25 电池盒2D图

（12）投放装置：投放盒便于包裹顺利投放至准确位置，储存盒用于储存包裹。电机转动，由横杆推动包裹向前，使包裹掉落，实现包裹的投放功能。其3D图和2D图如上文提及的图4-3所示和下图4-26所示。


图4-26 投放装置2D图

## 4.4 任务完成情况小结

在本次任务中，项目组对小车的整体结构设计提出建设性意见，王炳达提议用舵机控制投放的精度，郭法提议车身为两层结构更适合零件的布局与放置，周艺梵提议差速转向与推杆式投放，刘洋提议车轮分为两个转向前轮、两个万向后轮，王宗辉提出不同的零件连接方式。项目组进行讨论并采纳组员的不同方面的意见。

项目组对本次任务充满积极性并认真完成，王炳达负责投放与转向机构的设计，刘洋负责万向轮、驱动轮、舵机、投放电机、电机联轴器、电机驱动器、电机板、电机的设计，王宗辉负责Arduino开发板、传感器、电池盒、面包板的设计，郭法负责小车整体的3D模型建立、爆炸图的制作和零件的测量，周艺梵负责小车的最终草图手绘，2D图的绘制以及小组会议记录、工作小结、课程报告的撰写。

项目组成员认真完成本次任务，完成质量较高，在项目组成员绘制遇到困难的时候组长提供建议与解决措施，组员之间互相帮助，但是工作效率有待提高。

## 4.5 小组会议记录

“设计与建造”课程小组会议记录

议题 | “智能循迹派送小车”的项目产品详细设计
组长 | 王炳达 | | 年级/班级/组别 | | | 2021级二班第4组
组员 | 周艺梵、郭法、刘洋、王宗辉
会议时间 | | 2021年11月04日 20：00-22：00 | | 会议地点 | 郑东图书馆306读者研究厢
讨论内容 | | 1．讨论本次任务的分工，周艺梵负责最终概念草图的手绘，2D图绘制，课程报告、小组会议记录和小结的撰写，王炳达负责投放与转向机构的3D模型建立，王宗辉、刘洋负责小车零件的3D模型建立，郭法负责小车装配图的生成以及爆炸图的制作。 2．讨论智能派送车的整车结构，研究各个零件所放置的位置，分析怎样放置能够使小车平稳行驶。 3．认识各个零件，清点核实各个零件的数目，安排郭法保存零件。 4．详细讨论转向和投放机构的具体方案，最终确定转向为差速转向，投放为推杆式投放。
下一步工作计划 | | 1．在各成员完成任务后进行下一部分的分工。 2．讨论课程报告与PPT制作，在制作完成后统一讨论改进。 3．测量零件的尺寸，并进行3D模型建立。 4．报告完成后，进行Arduino编程的训练与电路设计的学习。
附件材料清单 | | 无

参会成员：王炳达 刘洋 郭法 王宗辉 周艺梵

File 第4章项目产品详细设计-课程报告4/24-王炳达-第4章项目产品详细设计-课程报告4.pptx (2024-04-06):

## 课程报告四

- 求是学部二班四组

- 汇报人：王炳达 王宗辉周艺梵 郭法 刘洋

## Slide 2

contents

1

配件选用
投放与转向机构设计
概念草图

王炳达
周艺梵

2

驱动系统设计

3

传感系统设计

4

整体模型建立
爆炸图

5

产品2D图
任务完成小结
会议记录

周艺梵

刘洋

王宗辉

郭法

## 配件选择 投放与转向机构 概念草图

01

- 负责人：周艺梵
- 王炳达

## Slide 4

手绘概念草图

对于智能派送车整车结构设计，项目组采用双层结构、前轮驱动模式、差速转向机构、推杆式投放机构。


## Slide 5

标准件及配件选用

项目组清点并核实智能派送车的标准件及配件，包括电池盒、驱动轮、万向轮、电机、电机驱动器、面包板、Arduino开发板、四路红外传感器以及若干铜柱。各个零件的具体数目和信息如表所示。

标准件及配件 | 数目 | 备注
电池盒 | 3 | 大电池盒2个，小电池盒1个
电机驱动器 | 2 | 选用L298N电机驱动模块
万向轮 | 2
驱动轮 | 2
电机 | 3 | 两种不同型号的减速电机
面包板 | 1
传感器 | 1 | 四路红外传感器
铜柱 | 若干 | 含多种型号
Arduino开发板 | 1

表4-1 标准件及配件清单

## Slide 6

转向机构设计

智能派送车的转向机构包含在驱动机构中，如图所示。驱动机构由电机、电机支架、电机驱动模块和驱动轮构成，电机驱动模块控制电机，在传感器感知压线信号后，电机提供不同转速，利用两驱动前轮的差速及万向后轮的配合进行急转或者缓转。


智能派送车转向机构设计

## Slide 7

投放机构设计
智能派送车的投放机构由电机、储存盒和投放盒构成，如图所示。下图中，左侧盒子为投放盒，投放盒放置在底板外并挖出空格，便于物块掉落；右侧盒子为储存盒，放置在底板上，用于储存物块。电机转动一周，由横杆推动物块向前，使物块掉落，实现物块的单次投放，之后循环这一过程完成所有投放任务。


智能派送车投放机构设计

## 驱动系统

- 负责人：刘洋

02

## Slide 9

电机：产生驱动转矩，作为动力源将电源的电能转化为机械能，通过传动装置或直接驱动车轮进行转动


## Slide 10

电机联轴器：联轴器将电机与旋转轴连接，通过旋转轴传递动力。

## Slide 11

电机板：固定电机与底板。


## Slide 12

舵机：舵机是一种角度伺服的驱动，可以精准控制角度实现投放物块的准确


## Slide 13

驱动轮：实现小车的循迹功能，并通过两轮的配合实现转向。


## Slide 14

万向轮：使小车后轮能够灵活地跟随前轮转弯，保证小车沿轨迹正常行进。


## 传感系统

- 负责人：王宗辉

03

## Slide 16

面包板：面包板上存在很多小插孔，可以省略焊接步骤，节省电路的组装时间，对于项目组智能派送车的电路连接十分重要。


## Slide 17

电池盒：储存作为电源的电池，将电池与外部零件分隔开，便于更好地提供电能。

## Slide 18

四路红外传感器：红外传感器电路设计相对简单，检测信息速度快且成本低。检测四个位置的路况信息，确定小车的循迹情况，能够较精准地确定小车相对轨迹黑线的位置，并保证小车能感知投放定位点，从而发出刹车命令。


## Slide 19

Arduino开发板：作为总控制系统，其可接收红外传感器信号、识别黑线信号以及控制驱动和投放装置。


## 整体模型建立 爆炸图

- 负责人：郭法

04

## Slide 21

项目产品整车结构设计
对于智能派送车整车结构设计，项目组采用双层结构、前轮驱动模式、差速转向机构、推杆式投放机构。
双层结构能够保证小车的空间充裕和零件的摆放整齐，驱动前轮利用两轮的速度差转向，双万向后轮保证小车的稳定性，投放利用舵机控制推杆的转动将物块推下，舵机可以控制精度保证物块的准确落地。
智能派送车的第一层，红外传感器位于车的前部，从车底盘探出，便于精准识别黑线。两个小电池盒对立放置在两侧，维持小车平衡。电机驱动器对应放在两驱动前轮上方，Arduino开发板放置在两电机驱动器之间。第二层放置大电池盒和面包板，便于杜邦线的连接整理。
零部件之间的连接方式分为插孔式连接、螺栓螺母连接、铜柱连接。其中驱动轮与驱动电机，投放箱与下底板之间为插孔式连接。电机支架与电机、电机支架与下底板、电机驱动模块与下底板、面包板与上底板、Arduino开发板与下底板之间为螺栓螺母连接。上下底板之间、传感器与下底板、万向轮与下底板之间为铜柱连接。


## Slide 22

智能派送车爆炸图
为方便查看装配体中各零件之间的装配关系以及各个零件的装配过程，项目组制作小车爆炸图，如图所示。在爆炸图中，零件按照装配关系偏离原来的装配位置，将复杂的小车结构清晰地呈现出来。


## 产品2D图 任务完成小结 会议记录

- 负责人：周艺梵

05

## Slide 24

项目产品2D图


Arduino开发板2D图

四路红外传感器2D图

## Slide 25


电机2D图


电机联轴器2D图

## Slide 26


电机板2D图


舵机2D图

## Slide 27


面包板2D图


驱动轮2D图

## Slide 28


万向轮2D图

电池盒2D图

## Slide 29


图4-25 投放装置2D图

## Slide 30

任务完成情况小结
在本次任务中，项目组对小车的整体结构设计提出建设性意见，王炳达提议用舵机控制投放的精度，郭法提议车身为两层结构更适合零件的布局与放置，周艺梵提议差速转向与推杆式投放，刘洋提议车轮分为两个转向前轮、两个万向后轮。项目组进行讨论并采纳组员的不同方面的意见。
王炳达负责投放与转向机构的设计，刘洋负责万向轮、驱动轮、舵机、投放电机、电机联轴器、电机驱动器、电机板、电机的设计，王宗辉负责Arduino开发板、传感器、电池盒、面包板的设计，郭法负责小车整体的3D模型建立、爆炸图的制作和零件的测量，周艺梵负责小车的最终草图手绘，2D图的绘制以及小组会议记录、工作小结、课程报告的撰写。
项目组成员认真完成本次任务，完成质量较高，在项目组成员绘制遇到困难的时候组长提供建议与解决措施，组员之间互相帮助，但是工作效率有待提高。

小组会议记录
参会成员：王炳达 刘洋 郭法 王宗辉 周艺梵

议题 | “智能循迹派送小车”的项目产品详细设计
组长 | 王炳达 | | 年级/班级/组别 | | | 2021级二班第4组
组员 | 周艺梵、郭法、刘洋、王宗辉
会议时间 | | 2021年11月04日 20：00-22：00 | | 会议地点 | 郑东图书馆306读者研究厢
讨论内容 | | 1．讨论本次任务的分工，周艺梵负责最终概念草图的手绘，2D图绘制，课程报告、小组会议记录和小结的撰写，王炳达负责投放与转向机构的3D模型建立，王宗辉、刘洋负责小车零件的3D模型建立，郭法负责小车装配图的生成以及爆炸图的制作。 2．讨论智能派送车的整车结构，研究各个零件所放置的位置，分析怎样放置能够使小车平稳行驶。 3．认识各个零件，清点核实各个零件的数目，安排郭法保存零件。 4．详细讨论转向和投放机构的具体方案，最终确定转向为差速转向，投放为推杆式投放。
下一步工作计划 | | 1．在各成员完成任务后进行下一部分的分工。 2．讨论课程报告与PPT制作，在制作完成后统一讨论改进。 3．测量零件的尺寸，并进行3D模型建立。 4．报告完成后，进行Arduino编程的训练与电路设计的学习。
附件材料清单 | | 无

## 感谢观看

- Thanks for watching

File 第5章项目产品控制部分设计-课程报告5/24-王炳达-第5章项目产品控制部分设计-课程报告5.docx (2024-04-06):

# 课程报告5 项目产品控制部分设计

## 5.1 控制系统构成与连线图

### 5.1.1 控制系统构成

项目组的控制系统包括Arduino开发板、红外传感器、电机驱动器、驱动电机、投放舵机。

（1）Arduino开发板：接收传感器识别路况的信号，对信号进行处理输出，控制电机驱动小车，使小车实现启动、循迹、制动、投放等多种功能。

（2）红外传感器：对路况进行检测，确定小车的行驶情况，精准地确定小车相对轨迹的位置，保证小车能够正常启动、感知三个投放定位点、在终点刹车。

（3）电机驱动器：将来自主机的电脉冲信号转化为电机的角信号，使电机按照特定方向旋转固定角度。

（4）驱动电机：将电源的电能转化为机械能，使驱动轮转动，智能派送车前行。

（5）投放舵机：小车识别到投放点，Arduino开发板准确输出信号，舵机旋转精准角度，转动曲柄，进而推动推杆，投放包裹。

机电控制系统的架构图能较好地体现各个部分之间的联系以及信号的转换，如图5-1所示。


图5-1 机电控制系统架构

### 5.1.2 控制系统接线图

项目组最终采用双轮驱动、差速转向、舵机兼推杆式投放。驱动轮分别由两个电机驱动，两个电机驱动器L298N分别负责驱动两个电机。本项目中左驱动轮电机驱动器四个引脚（IN1、IN2、IN3、IN4）分别与Arduino开发板的0、1、2、3数字端口连接，端ENA、ENB接跳线帽，输出A（OUT1、OUT2）与左前轮电动机连接；右驱动轮与上述相似但其引脚（IN1、IN2、IN3、IN4）分别与Arduino开发板的13、12、11、8数字端口连接。电机驱动器与Arduino开发板共地并与12V电源的正负极相连。本项目采用舵机控制投放包裹的转动角度，舵机的控制线与Arduino开发板的9号管脚（有PWM波输出功能）相接，两根电源与12V电源的正负极相连。传感器与Arduino开发板相连，其中VCC、X1、X2、X3、X4分别与5V、A4、A3、A2、A1接口相连，二者共地。12V电源与舵机和电机驱动器间部分通过面包板连接。调试时Arduino开发板和传感器由大脑通过USB供电，实际运行时单片机另加5V电源。最终接线图如图5-2所示。

小车控制系统原理图

图5-2 智能派送小车的控制系统接线图

## 5.2 控制流程图

控制流程图表示一个过程中所有基本模块执行的可能流向，能够反映一个过程的实时执行过程。项目组的控制流程图基于各模块之间的相互关系、动态执行状态、各基本模块对应的语句表所绘制，如图5-3所示。

首先进行程序初始化，定义单片机各管脚的输入、输出属性，然后进入主循环。在主循环中，不断扫描传感器上四个光电管的状态，如果发现车辆轻微左偏或右偏，则向右或向左缓转来调整。如果发现车辆严重左偏或右偏，则向右或左急转来调整。如果检测到四个光电管全部处于黑色轨道线上，判断到达投放标记处，触发投放机构并计数一次。计数至第四次，判断到达终点，停车。除上述情况外，车辆保持直行。

初始化

检查传感器信号

1011或0111

1101或1110

左转

右转

0000

计数≥3

停止，结束

投放包裹

计数+1

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
图5-3 控制流程图

## 5.3 控制算法与实现

Arduino采用了开放源代码的软硬件平台，建构于简易输出和输入面板，适合智能派送车的简易编程。项目组采用Arduino软件进行编程，反复测试，确定最终方案，如图5-4、图5-5、图5-6所示。


图5-4 Arduino编程图1


图5-5 Arduino编程图2


图5-6 Arduino编程图3

## 5.4 任务完成情况小结

在本次任务中，项目组对智能派送车的控制部分设计的相关软件进行学习、交流讨论并且进行了实际操作。

项目组对本次任务充满积极性并认真完成，郭法负责控制系统接线图的绘制与说明，王宗辉负责控制策略流程图与会议记录，刘洋和王炳达负责控制算法编程，周艺梵负责控制元器件的详细说明、PPT的制作、任务完成情况小结和课程报告的撰写。

项目组成员认真完成本次任务，完成质量较高，成员之间互相讨论交流，提出工作改进方案，工作效率较上次有所提高。

## 5.5 小组会议记录

“设计与建造”课程小组会议记录

议题 | “智能循迹派送小车”的机电控制设计
组长 | 王炳达 | | 年级/班级/组别 | | | 2021级二班第4组
组员 | 周艺梵、郭法、刘洋、王宗辉
会议时间 | | 2021年11月19日 20：00-22：00 | | 会议地点 | 郑东图书馆209读者研究厢
讨论内容 | | 1．讨论本次任务的分工。郭法负责控制系统接线图的绘制与说明，王宗辉负责控制策略流程图与会议记录，刘洋和王炳达负责控制算法编程，周艺梵负责控制元器件的详细说明、PPT的制作、任务完成情况小结和课程报告的撰写。 2．讨论智能派送车的电路接线设计，研究各个导线插孔的位置，分析讨论正确的连接方式。 3．进行小车零件的性能测试与初步组装，从小车的初步行驶中对设计进行改进。 4．详细讨论编程的各个模块代码，确定最终计数次数，改进方案，使小车循迹投放精准化。
下一步工作计划 | | 1．在各成员完成任务后进行下一部分的分工。 2．讨论课程报告与PPT制作，在制作完成后统一讨论改进。 3．进行硬件的初步连接与性能测试。 4．规划3D打印部件的制作以及整车的初装。
附件材料清单 | | 见附录A 智能派送车零件尺寸 见附录B 智能派送车上下底板CAD图

参会成员：王炳达 刘洋 郭法 王宗辉 周艺梵

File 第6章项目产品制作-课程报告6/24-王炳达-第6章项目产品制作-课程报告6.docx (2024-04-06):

# 课程报告6 项目产品制作

## 6.1 零件毛坯材料及规格

### 6.1.1 零件毛坯材料

项目组选用的零件毛坯材料包括：

（1）送轮类：驱动轮、万向轮。

（2）轴类：铜柱、电机连轴器。

（3）支架类：亚克力板、万向轮支撑板、面包板。

（4）箱体类：3D打印投放装置、12V电池盒、5V电池盒。

（5）其他类：Arduino开发板、红外传感器、电机驱动器、电机。

### 6.1.2 零件毛坯规格

项目组对所选用的零件进行了测量，具体规格如表6-1所示。

表6-1 智能派送车的零件毛坯规格

零件名称 | 长（mm） | 宽（mm） | 高（mm） | 材料 | 其他（mm） | 数量
驱动轮 | 65 | 25 | 65 | | 接口直径：6 | 2
万向轮 | 24 | 13 | 24 | | 内凹深度：5 | 2
电机连轴器 | 10 | 10 | 12 | | 六棱柱棱长：7 六棱柱高：5 | 2
亚克力板 | 303 | 299 | 2 | | | 1
万向轮板 | 38 | 33 | 1 | | 圆孔直径：4 | 1
面包板 | 163 | 54 | 8 | | | 1
投放装置 | 140 | 82 | 31 | PLA | | 1
12V电池盒 | 126 | 72 | 19 | | | 1
5V电池盒 | 95 | 74 | 19 | | | 1
Arduino开发板 | 79 | 57 | 19 | | | 1
红外传感器 | 70 | 18 | 1 | | 小圆柱直径：5 小圆柱高度：10 | 1
电机驱动器 | 43 | 43 | 26 （最高） | | | 2
电机 | 36 | 36 | 22 | | 胖轴高度：6 胖轴直径：11 细轴高度：15 细轴直径：5 | 2

## 6.2 投放装置制作过程

项目组对投放装置进行3D打印，通过对零件的CAD数据分层处理，得到二维截面数据，并使用PLA材料逐层累加，最终投放装置成型。投放装置分为四个部分，分别是载物盒与投放盒（如图6-1所示）、连杆一（如图6-2所示）、连杆二（如图6-3所示）、连杆三（如图6-4所示）。


图6-1 载物盒与投放盒


图6-2 连杆一


图6-3 连杆二


图6-4 连杆三

## 6.3 项目产品装配

项目组对小车的装配布局进行规划和改进，具体装配步骤如下：

（1）项目组对底板划线并对底板进行激光打孔切割。

（2）对零件进行组装，将驱动轮与电机通过电机联轴器连接，万向轮与万向轮支撑板用螺栓螺母连接。将两个驱动轮用螺栓螺母固定在小车下底板的左前方和右前方，两个万向轮用螺栓螺母固定在小车下底板的左后方和右后方。

（3）上底板与下底板之间通过四个铜柱连接。

（4）将红外传感器用螺栓螺母固定在小车下底板的正前方。

（5）将投放舵机安装在小车下底板的中部，投放装置安装在小车下底板的后部。

（6）将电池盒与面包板安装在小车的上底板，并对各个部分完成线路连接工作。

## 6.4 任务完成小结

在本次任务中，项目组对各部分材料和零件进行研究，并且实际动手操作，对小车的各部分进行组装。

项目组认真完成本次任务，工作效率较上次有所提高。郭法负责零件毛坯材料和规格的确定并列出详细表单，王炳达记录投放装置的制作过程并完成会议记录的撰写，王宗辉负责记录项目产品的装配过程，周艺梵完成任务小结和课程报告，刘洋负责PPT的制作。

项目组成员积极参与小车制作过程，完成质量较高。周艺梵、郭法完成底板的激光切割，刘洋、王炳达、王宗辉完成投放装置的3D打印。最终各成员协调配合、团结一致，完成小车各个部分的拼装与连接。

## 6.5 小组会议记录

“设计与建造”课程小组会议记录

议题 | “智能循迹派送小车”的各部分材料与组装
组长 | 王炳达 | | 年级/班级/组别 | | | 2021级二班第4组
组员 | 周艺梵、郭法、刘洋、王宗辉
会议时间 | | 2021年11月30日 20：00-22：00 | | 会议地点 | 第35教学楼智能制造中心
讨论内容 | | 1．讨论本次任务的分工。郭法负责零件毛坯材料和规格的确定，并列出详细表单；王炳达负责记录投放装置的制作过程和会议记录的撰写；王宗辉主要负责项目产品的装配，其他成员辅助；周艺梵负责任务完成小结和课程报告；刘洋负责PPT的制作。 2．讨论各成员任务的具体注意事项和详细步骤，并规定各部分任务的完成时间。 3．讨论并确定智能派送车的具体组装方案和各零件的安装方法。 4．讨论并确定智能派送车的代码流程，对转向的急转和缓转代码改进，并由刘洋和王炳达完成代码在运行前的最后一次修改。 5．对底板的打孔方法做出最终决定，通过比较激光打孔和手动钻孔的难易程度与准确性，项目组决定采取先激光打孔定位再手动钻孔改进孔径大小的方式。
下一步工作计划 | | 1．在各成员完成任务后进行下一部分的分工，并且按照小组成员的分工完成整车的组装。 2．完成智能派送车的调试。 3．讨论课程报告与PPT制作，在制作完成后统一讨论改进。 4．确定下一次会议时间。
附件材料清单 | | 见附录A 智能派送车零件尺寸 见附录B 智能派送车上下底板CAD图

参会成员：王炳达 刘洋 郭法 王宗辉 周艺梵

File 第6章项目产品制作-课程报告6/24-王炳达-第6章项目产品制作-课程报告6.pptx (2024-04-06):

## 课程报告六

- 求是学部二班4组

- 汇报人：王炳达 王宗辉周艺梵 郭法 刘洋

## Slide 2

contents

1

零件毛坯材料及规格

2

投放装置
制作过程

王炳达

3

项目产品装配

4

会议记录

5

完成情况小结

郭法

王宗辉

王炳达

周艺梵

## 零件毛坯材料及规格

01

- 负责人：郭法

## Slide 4

零件毛坯材料

项目组选用的零件毛坯材料包括：
（1）送轮类：驱动轮、万向轮。
（2）轴类：铜柱、电机连轴器。
（3）支架类：亚克力板、万向轮支撑板、面包板。
（4）箱体类：3D打印投放装置、12V电池盒、5V电池盒。
（5）其他类：Arduino开发板、红外传感器、电机驱动器、电机。

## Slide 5

零件毛坯规格

项目组对所选用的零件进行了测量，具体规格如表所示

零件名称 | 长（mm） | 宽（mm） | 高（mm） | 材料 | 其他（mm） | 数量
驱动轮 | 65 | 25 | 65 | | 接口直径：6 | 2
万向轮 | 24 | 13 | 24 | | 内凹深度：5 | 2
电机连轴器 | 10 | 10 | 12 | | 六棱柱棱长：7 六棱柱高：5 | 2
亚克力板 | 303 | 299 | 2 | | | 1
万向轮板 | 38 | 33 | 1 | | 圆孔直径：4 | 1
面包板 | 163 | 54 | 8 | | | 1
投放装置 | 140 | 82 | 31 | PLA | | 1
12V电池盒 | 126 | 72 | 19 | | | 1
5V电池盒 | 95 | 74 | 19 | | | 1
Arduino开发板 | 79 | 57 | 19 | | | 1
红外传感器 | 70 | 18 | 1 | | 小圆柱直径：5 小圆柱高度：10 | 1
电机驱动器 | 43 | 43 | 26（最高） | | | 2
电机 | 36 | 36 | 22 | | 胖轴高度：6 胖轴直径：11 细轴高度：15 细轴直径：5 | 2

## 投放装置制作过程

- 负责人：王炳达

02

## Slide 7

项目组对投放装置进行3D打印，通过对零件的CAD数据分层处理，得到二维截面数据，并使用PLA材料逐层累加，最终投放装置成型。投放装置分为四个部分，分别是载物盒与投放盒、连杆一、连杆二、连杆三。


载物盒与投放盒


连杆一

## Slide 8


连杆二

连杆三

## 项目产品装配

- 负责人：王宗辉

03

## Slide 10

项目组对小车的装配布局进行规划和改进，具体装配步骤如下：
（1）项目组对底板划线并对底板进行激光打孔切割。
（2）对零件进行组装，将驱动轮与电机通过电机联轴器连接，万向轮与万向轮支撑板用螺栓螺母连接。将两个驱动轮用螺栓螺母固定在小车下底板的左前方和右前方，两个万向轮用螺栓螺母固定在小车下底板的左后方和右后方。
（3）上底板与下底板之间通过四个铜柱连接。
（4）将红外传感器用螺栓螺母固定在小车下底板的正前方。
（5）将投放舵机安装在小车下底板的中部，投放装置安装在小车下底板的后部。
（6）将电池盒与面包板安装在小车的上底板，并对各个部分完成线路连接工作。

## 会议记录

- 负责人：王炳达

04

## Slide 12

会议记录


## 任务完成情况小结

- 负责人：周艺梵

05

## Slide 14

在本次任务中，项目组对各部分材料和零件进行研究，并且实际动手操作，对小车的各部分进行组装。
项目组认真完成本次任务，工作效率较上次有所提高。郭法负责零件毛坯材料和规格的确定并列出详细表单，王炳达记录投放装置的制作过程并完成会议记录的撰写，王宗辉负责记录项目产品的装配过程，周艺梵完成任务小结和课程报告，刘洋负责PPT的制作。
项目组成员积极参与小车制作过程，完成质量较高。周艺梵、郭法完成底板的激光切割，刘洋、王炳达、王宗辉完成投放装置的3D打印。最终各成员协调配合、团结一致，完成小车各个部分的拼装与连接。

## 感谢观看

- Thanks for watching

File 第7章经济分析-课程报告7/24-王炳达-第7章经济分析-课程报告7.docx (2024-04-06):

# 课程报告7 经济分析

## 7.1 项目产品开发经济分析

### 7.1.1 经济分析要素

小车的项目经济分析模型主要考虑以下六个因素：

（1）销售收入：价格乘以销量获得的数据。

（2）生产启动成本：3D打印和激光打孔等设备购买和装备费用以及项目投资建设初期费用等。

（3）生产成本：小车材料和零件购买费用，激光打孔加工费用，电池消耗费用，研发人员费用、实验费用、试制费用等。

（4）质量问题：小车的使用年限、运送效率以及更换成本等。

（5）市场营销和辅助成本分析：广告宣传以及渠道、物流等费用。

（6）开发时间：从项目的初步设计到具体细节的设计再到最终开发和组装的开发周期。

项目组认为智能派送小车尚未投入市场，生产营销费用和销售收入难以评估，且生产启动成本随着客观条件的变化而变化，故放弃对上述模型的分析。最终，项目组选择了生产成本、小车质量和开发时间作为分析对象。

### 7.1.2 智能派送小车的经济分析

经项目组的认真分析，智能派送小车的经济分析具体如下：

（1）成本分析：小车由上下两个亚克力板组成，两个驱动轮和电机及L298N 构成驱动系统，循迹主要由四路红外传感器组成，舵机和投放装置构成投放模块，Arduino开发板主要负责控制整车运行情况，大电池盒和小电池盒内分别装有九节和六节5V碱性电池，同时使用了万向轮和一些连接部件。项目组在评估零件费用，加工费用和研发费用后，预估整车的成本在400～450元。

（2）质量分析：小车最终承重存在缺陷，因此亚克力板需要及时更换；四个轮子在实际应用中会出现磨损，需要及时维护；电池的电量有限，供电不足会影响运行效率，也需要定时更换。

（3）开发时间分析：项目组对小车的初步设计用了近五周时间，具体的设计和细节历时两周，最终组装花费近四周时间。项目开发周期较短，值得开发。

## 7.2 项目产品开发对社会的影响

智能派送车进入市场将对快递和运输等行业带来革命性的影响：

（1）能够解放劳动力，有利于劳动力的转型升级。

（2）降低快递公司的派送成本，提高派送效率，有利于降低快递价格和提高快递公司经济收入。

（3）使快递运往一些地势复杂、经济落后的偏远地区更加便捷。

（4）若快速大范围应用，有可能造成一定的失业问题。

## 7.3 任务完成情况小结

在本次任务中，项目组对智能派送车的设计与制作进行了经济成本分析，以及产品开发带来的经济效益与社会影响分析。

项目组认真完成本次任务，团队协作效率逐渐提高。郭法负责产品开发经济分析，王炳达分析项目产品开发对社会的影响，王宗辉负责任务完成小结与会议记录的书写，周艺梵负责课程报告的书写，刘洋负责PPT的制作。

## 7.4 小组会议记录

“设计与建造”课程小组会议记录

议题 | “智能循迹派送小车”的经济分析
组长 | 王炳达 | | 年级/班级/组别 | | | 2021级二班第4组
组员 | 周艺梵、郭法、刘洋、王宗辉
会议时间 | | 2021年12月20日 20：00-22：00 | | 会议地点 | 第35教学楼智能制造中心
讨论内容 | | 1．讨论本次任务的分工。郭法负责产品开发经济分析，王炳达分析项目产品开发对社会的影响，王宗辉负责任务完成小结与会议记录的书写；周艺梵负责课程报告的书写，刘洋负责PPT的制作。 2．讨论各成员任务的具体注意事项和详细步骤，并规定各部分任务的完成时间。 3．广泛查阅资料，对智能派送车的制作成本进行进一步的分析，同时联系产品开发对社会的影响，进而对智能派送车提出改进意见。 4．对智能派送车的功能进行改进与完善。
下一步工作计划 | | 1．在各成员完成任务后进行下一部分的分工，并且按照小组成员的分工完成整车的组装。 2．完成智能派送车的调试。 3．对智能派送车进行多次实验，争取改善智能派送车的循迹精度与投放精度，并缩短完成时间。
附件材料清单 | | 无

参会成员：王炳达 刘洋 郭法 王宗辉 周艺梵

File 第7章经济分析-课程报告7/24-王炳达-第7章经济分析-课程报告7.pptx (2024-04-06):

## 课程报告七

- 求是学部二班4组

- 汇报人：王炳达 王宗辉周艺梵 郭法 刘洋

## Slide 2

contents

1

项目产品开发经济分析

2

项目产品开发对社会的影响

王炳达

3

会议记录

4

完成情况小结

郭法

王宗辉

王宗辉

## 项目产品开发经济分析

01

- 负责人：郭法

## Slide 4

经济分析要素
小车的项目经济分析模型主要考虑以下六个因素：
（1）销售收入：价格乘以销量获得的数据。
（2）生产启动成本：3D打印和激光打孔等设备购买和装备费用以及项目投资建设初期费用等。
（3）生产成本：小车材料和零件购买费用，激光打孔加工费用，电池消耗费用，研发人员费用、实验费用、试制费用等。
（4）质量问题：小车的使用年限、运送效率以及更换成本等。
（5）市场营销和辅助成本分析：广告宣传以及渠道、物流等费用。
（6）开发时间：从项目的初步设计到具体细节的设计再到最终开发和组装的开发周期。
项目组认为智能派送小车尚未投入市场，生产营销费用和销售收入难以评估，且生产启动成本随着客观条件的变化而变化，故放弃对上述模型的分析。最终，项目组选择了生产成本、小车质量和开发时间作为分析对象。

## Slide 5

智能派送小车的经济分析
经项目组的认真分析，智能派送小车的经济分析具体如下：
（1）成本分析：小车由上下两个亚克力板组成，两个驱动轮和电机及L298N 构成驱动系统，循迹主要由四路红外传感器组成，舵机和投放装置构成投放模块，Arduino开发板主要负责控制整车运行情况，大电池盒和小电池盒内分别装有九节和六节5V碱性电池，同时使用了万向轮和一些连接部件。项目组在评估零件费用，加工费用和研发费用后，预估整车的成本在400～450元。
（2）质量分析：小车最终承重存在缺陷，因此亚克力板需要及时更换；四个轮子在实际应用中会出现磨损，需要及时维护；电池的电量有限，供电不足会影响运行效率，也需要定时更换。
（3）开发时间分析：项目组对小车的初步设计用了近五周时间，具体的设计和细节历时两周，最终组装花费近四周时间。项目开发周期较短，值得开发。

## 项目产品开发对社会的影响

02

- 负责人：王炳达

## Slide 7

智能派送车进入市场将对快递和运输等行业带来革命性的影响：
（1）能够解放劳动力，有利于劳动力的转型升级。
（2）降低快递公司的派送成本，提高派送效率，有利于降低快递价格和提高快递公司经济收入。
（3）使快递运往一些地势复杂、经济落后的偏远地区更加便捷。
（4）若快速大范围应用，有可能造成一定的失业问题。

## 会议记录

- 负责人：王宗辉

03

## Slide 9


会议记录
如右图所示

## 完成情况小结

- 负责人：王宗辉

04

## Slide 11

7.3 任务完成情况小结
在本次任务中，项目组对智能派送车的设计与制作进行了经济成本分析，以及产品开发带来的经济效益与社会影响分析。
项目组认真完成本次任务，团队协作效率逐渐提高。郭法负责产品开发经济分析，王炳达分析项目产品开发对社会的影响，王宗辉负责任务完成小结与会议记录的书写，周艺梵负责课程报告的书写，刘洋负责PPT的制作。

## 感谢观看

- Thanks for watching

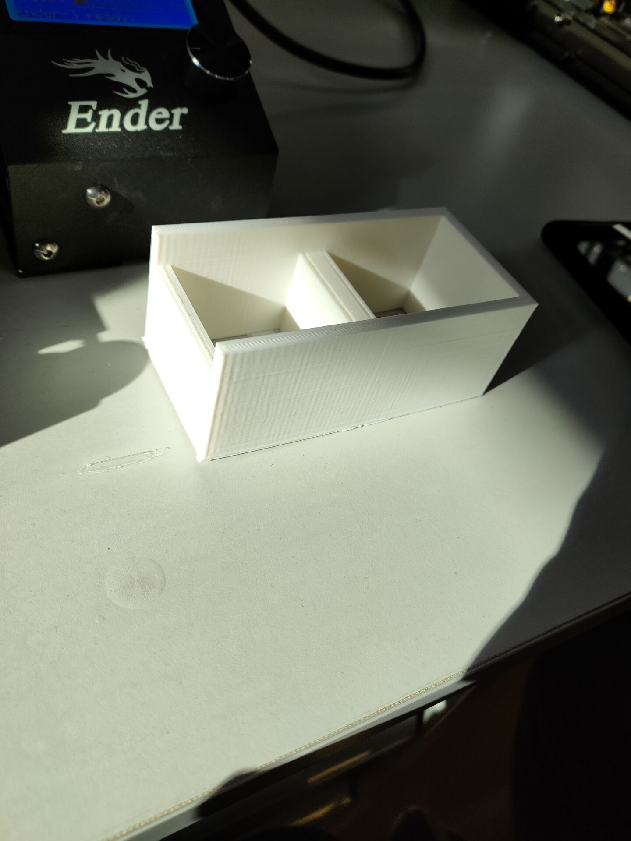
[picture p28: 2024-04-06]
deliver device.jpg

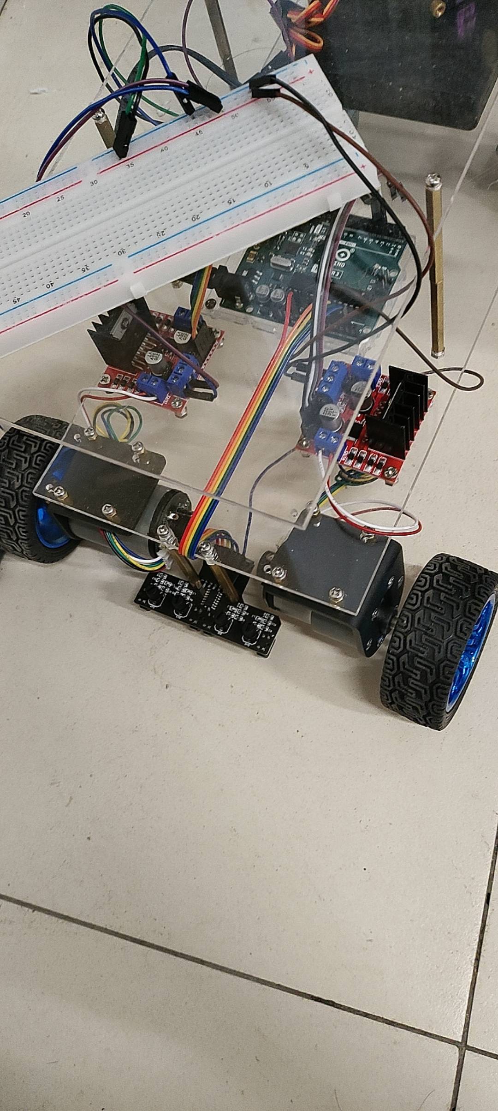
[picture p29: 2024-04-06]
电路连接图.jpg

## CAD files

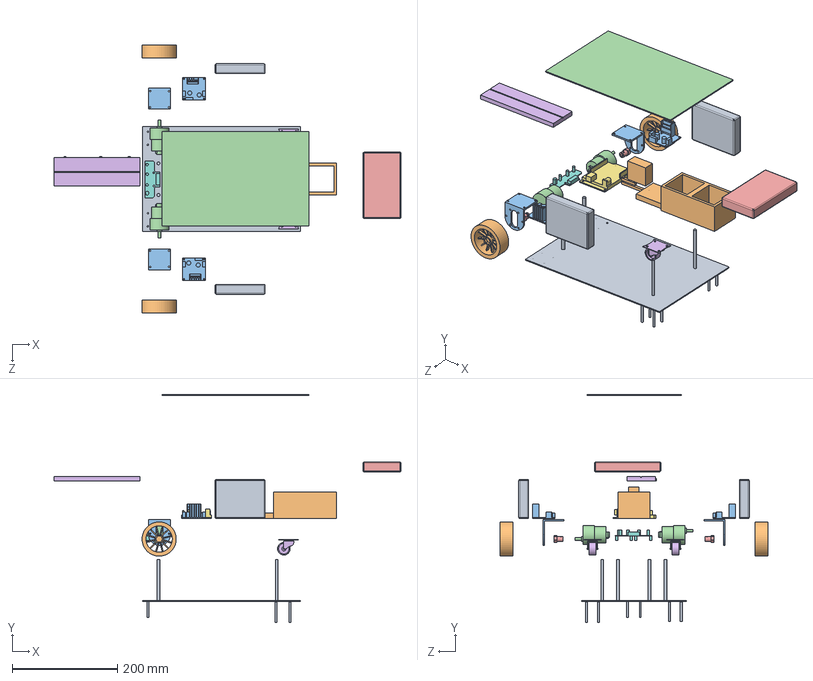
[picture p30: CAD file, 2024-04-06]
零件图/智能派送小车模型.SLDASM
659.6 x 433.6 x 509.6 mm
diban
驱动轮 x 2
电机板 x 2
电机 x 2
电机联轴器 x 2
万向轮及其配件 x 2
arduino电路板
传感器(1)
小电池盒 x 2
投放与安置器
电机驱动器 x 2
底板
大电池盒
面包板

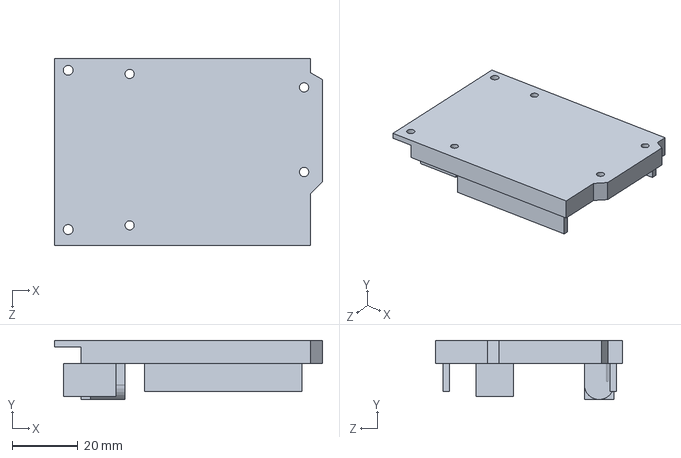
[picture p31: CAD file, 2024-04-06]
零件图/arduino电路板.SLDPRT
81.6 x 18.0 x 57.0 mm

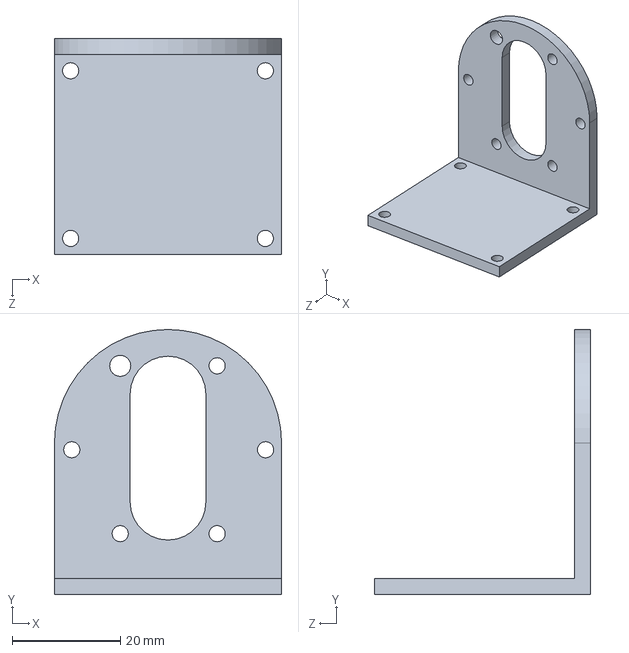
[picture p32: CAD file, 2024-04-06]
零件图/电机板.SLDPRT
42.0 x 49.0 x 40.0 mm

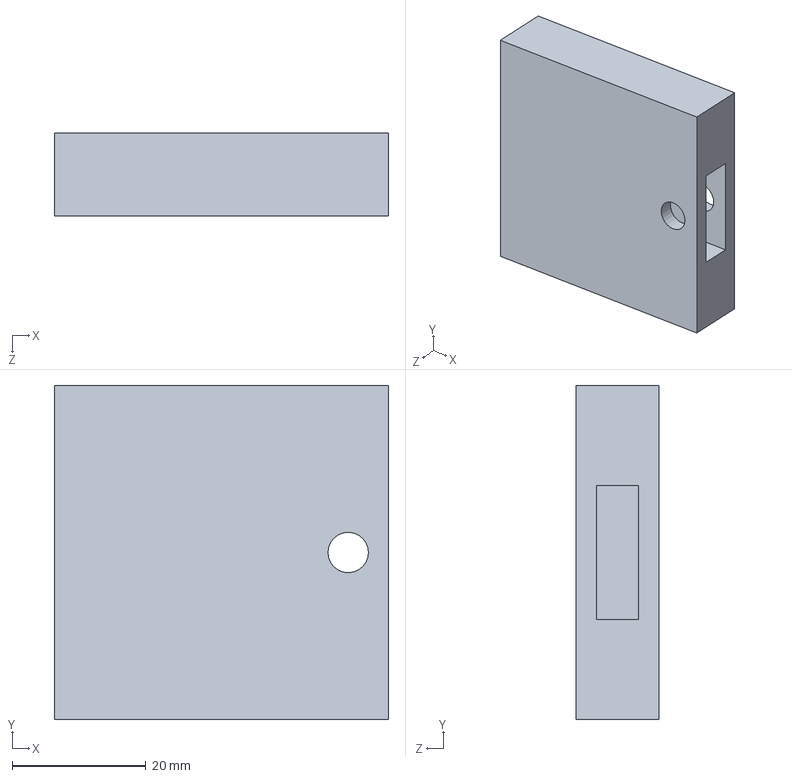
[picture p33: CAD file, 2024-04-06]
零件图/投放零件2.SLDPRT
50.0 x 50.0 x 12.4 mm

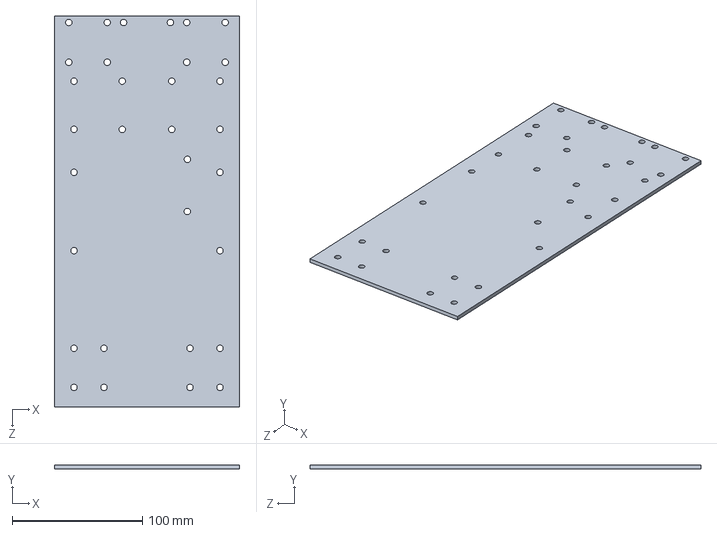
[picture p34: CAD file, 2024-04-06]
零件图/下底板.SLDPRT
142.0 x 3.00 x 300.0 mm

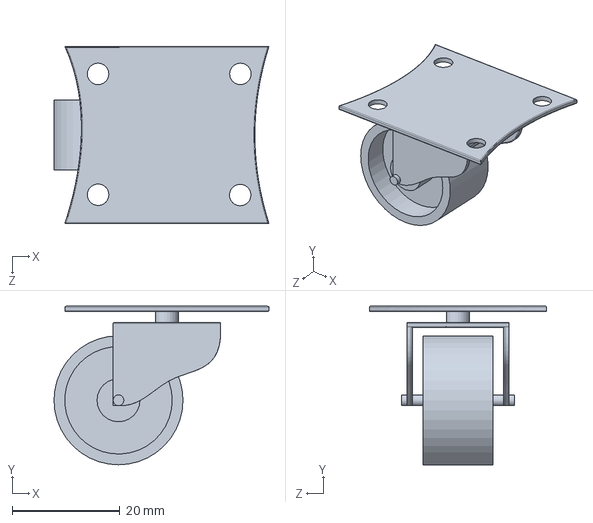
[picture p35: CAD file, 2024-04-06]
零件图/万向轮及其配件.SLDPRT
40.0 x 29.5 x 33.0 mm

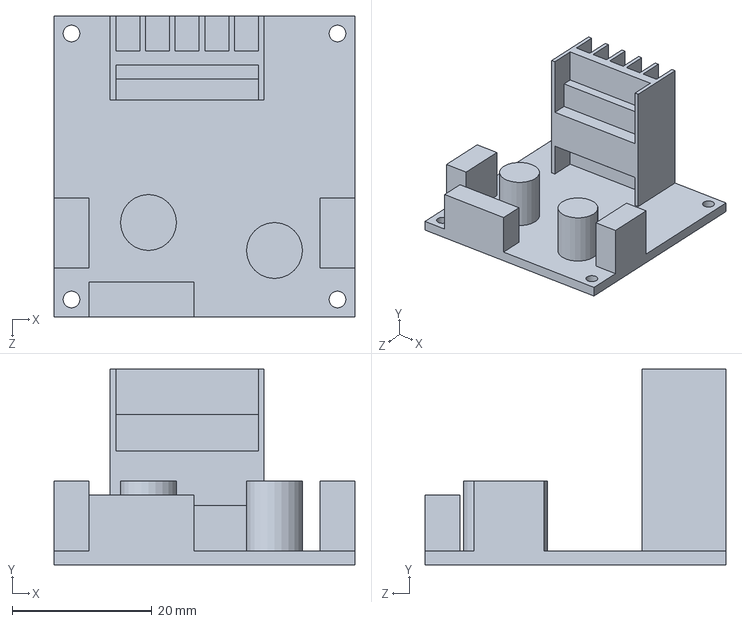
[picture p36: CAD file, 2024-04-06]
零件图/电机驱动器.SLDPRT
43.0 x 28.0 x 43.0 mm

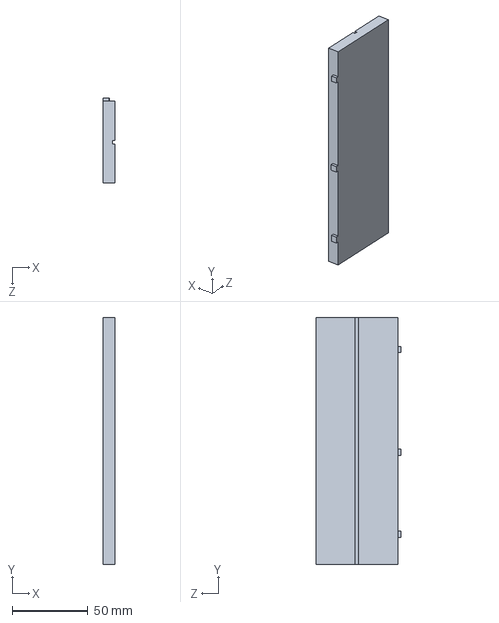
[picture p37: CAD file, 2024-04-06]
零件图/面包板.SLDPRT
8.00 x 163.0 x 56.0 mm

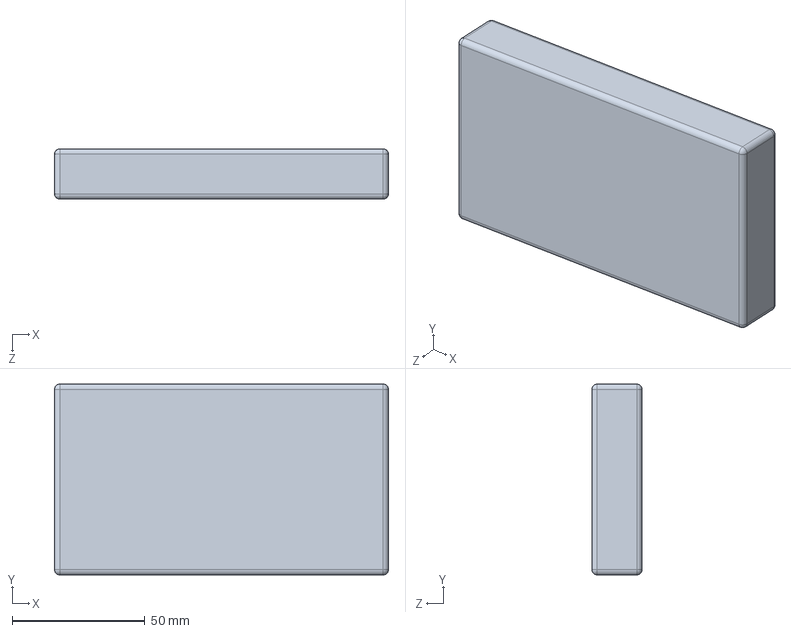
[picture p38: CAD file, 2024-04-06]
零件图/大电池盒.SLDPRT
126.0 x 72.0 x 19.0 mm

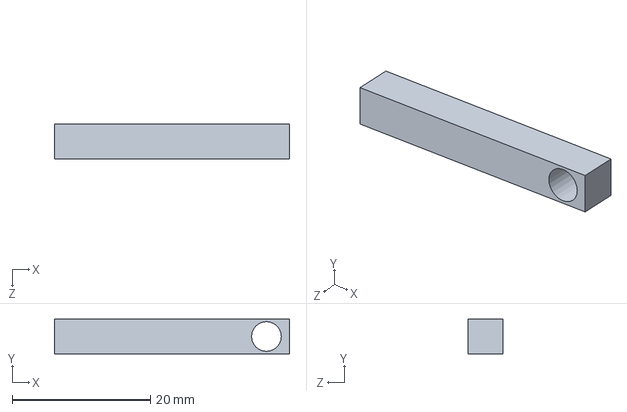
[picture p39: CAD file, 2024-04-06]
零件图/投放零件3.SLDPRT
34.0 x 5.00 x 5.00 mm

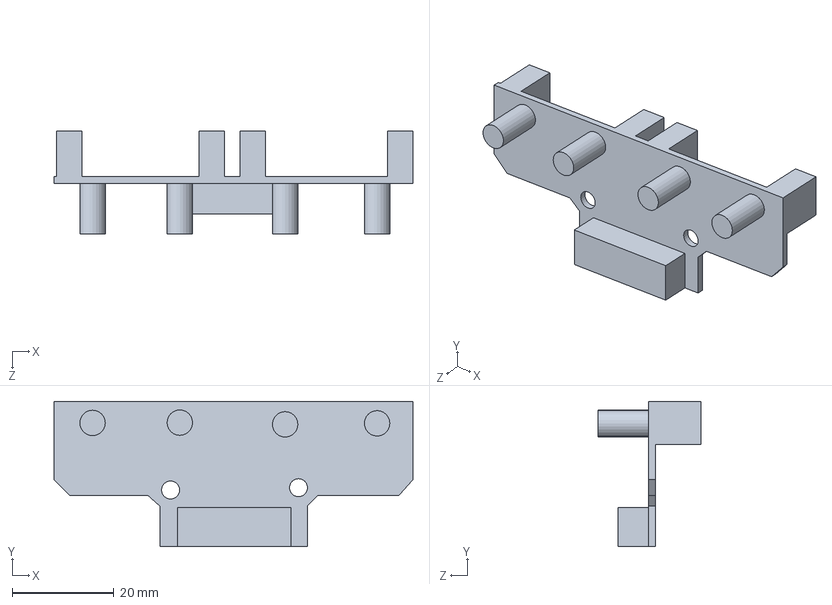
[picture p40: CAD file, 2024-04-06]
零件图/传感器(1).SLDPRT
70.5 x 28.5 x 20.3 mm

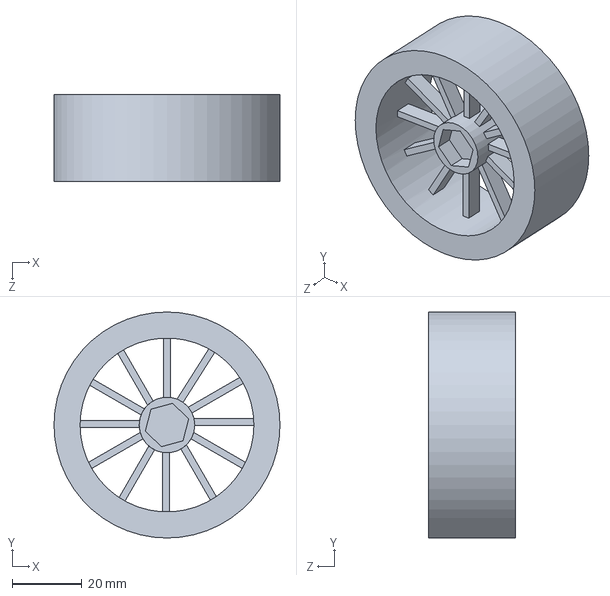
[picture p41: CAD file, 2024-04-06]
零件图/驱动轮.SLDPRT
65.0 x 65.0 x 25.0 mm

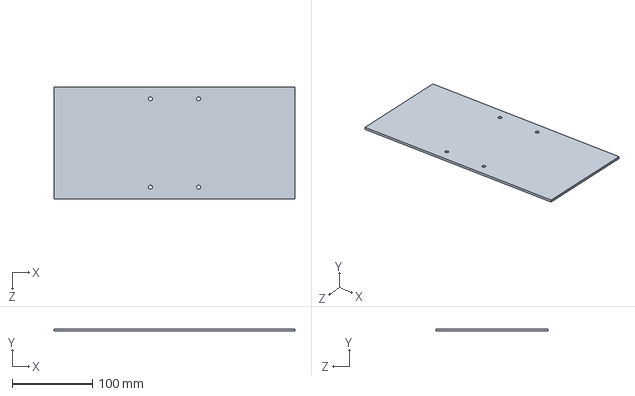
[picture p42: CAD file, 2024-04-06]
零件图/上底板.SLDPRT
300.0 x 3.00 x 140.0 mm

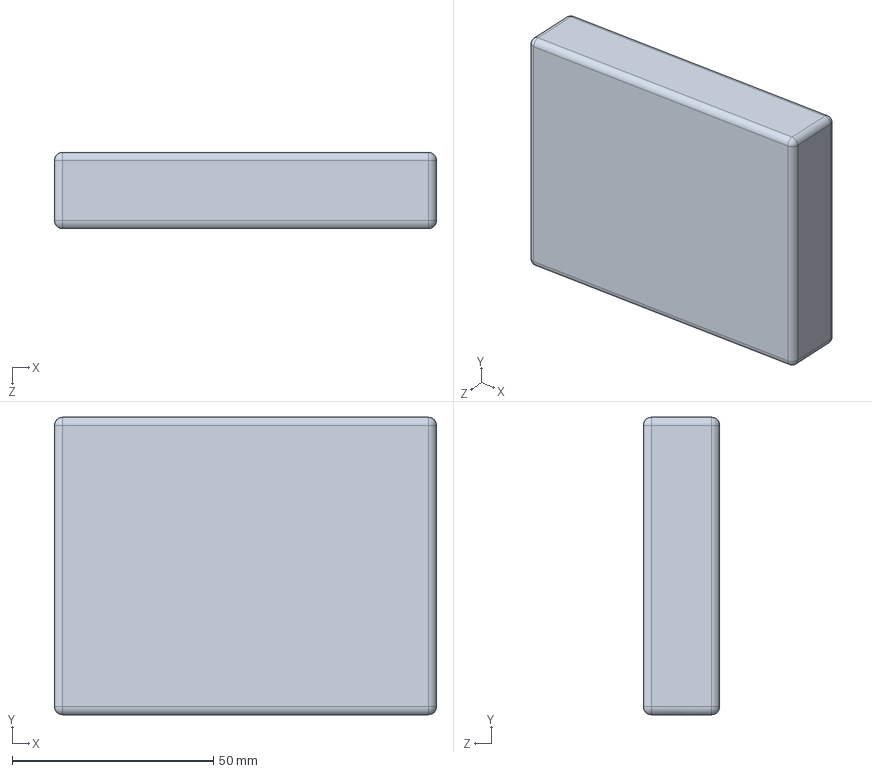
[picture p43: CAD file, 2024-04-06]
零件图/小电池盒.SLDPRT
95.0 x 74.0 x 19.0 mm

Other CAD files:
零件图/电机联轴器.SLDPRT
零件图/投放与安置器.SLDPRT
零件图/舵机.SLDPRT
零件图/投放零件1.SLDPRT
工程图/工程图sw/arduino电路板.SLDDRW
工程图/工程图sw/万向轮及其配件.SLDDRW
工程图/工程图sw/上底板.SLDDRW
工程图/工程图sw/下底板.SLDDRW
工程图/工程图sw/四路传感器.SLDDRW
工程图/工程图sw/大电池盒.SLDDRW
工程图/工程图sw/投放与安置器.SLDDRW
工程图/工程图sw/投放零件1.SLDDRW
工程图/工程图sw/投放零件2.SLDDRW
工程图/工程图sw/投放零件3.SLDDRW
工程图/工程图sw/智能派送小车模型.SLDDRW
工程图/工程图sw/电机.SLDDRW
工程图/工程图sw/电机板.SLDDRW
工程图/工程图sw/电机联轴器.SLDDRW
工程图/工程图sw/舵机.SLDDRW
工程图/工程图sw/面包板.SLDDRW
工程图/工程图sw/驱动轮.SLDDRW
零件图/电机.SLDPRT

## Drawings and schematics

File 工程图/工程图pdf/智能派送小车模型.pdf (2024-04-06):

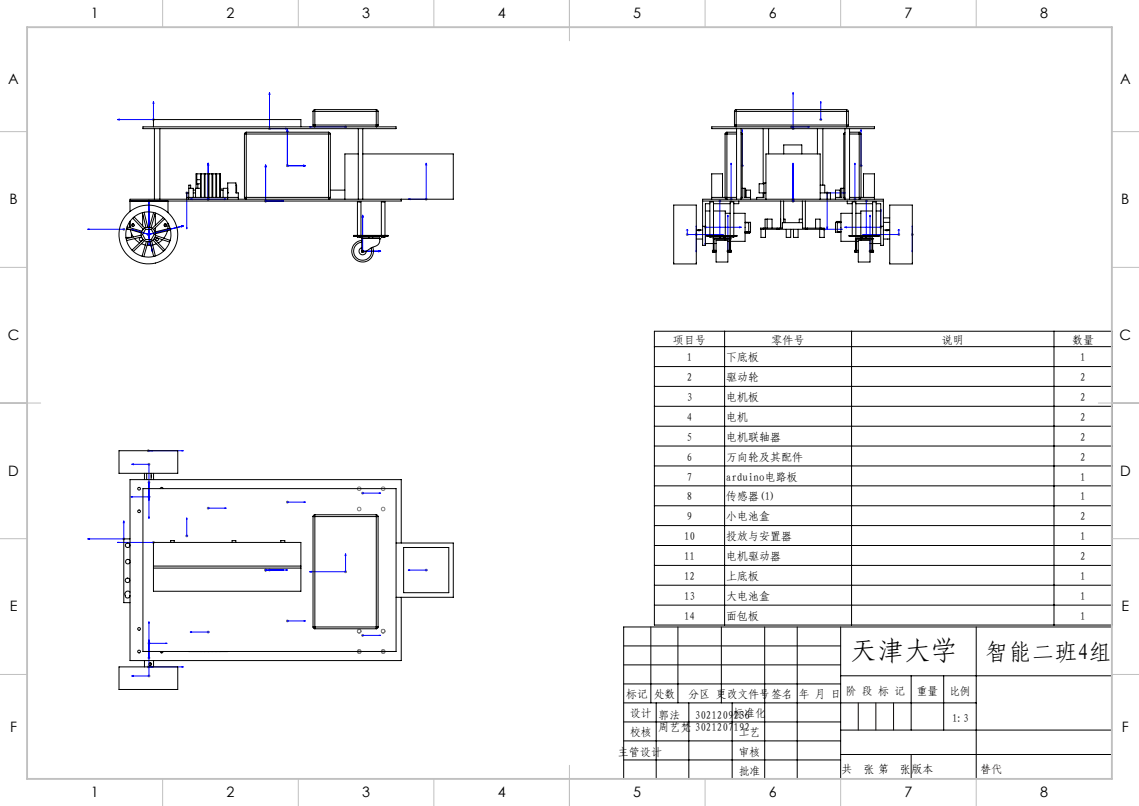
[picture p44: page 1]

项目号 | 零件号 | 说明 | 数量
1 | 下底板 | | 1
2 | 驱动轮 | | 2
3 | 电机板 | | 2
4 | 电机 | | 2
5 | 电机联轴器 | | 2
6 | 万向轮及其配件 | | 2
7 | arduino电路板 | | 1
8 | 传感器(1) | | 1
9 | 小电池盒 | | 2
10 | 投放与安置器 | | 1
11 | 电机驱动器 | | 2
12 | 上底板 | | 1
13 | 大电池盒 | | 1
14 | 面包板 | | 1

天津大学 | 智能二班4组

标记 | 处数 | 分区 更改文件号签名 | | 年 月 日
设计 | 郭法 | 3021209236 | 标准化 | | 1:3
校核 | 周艺梵 | 3021207192 | 工艺

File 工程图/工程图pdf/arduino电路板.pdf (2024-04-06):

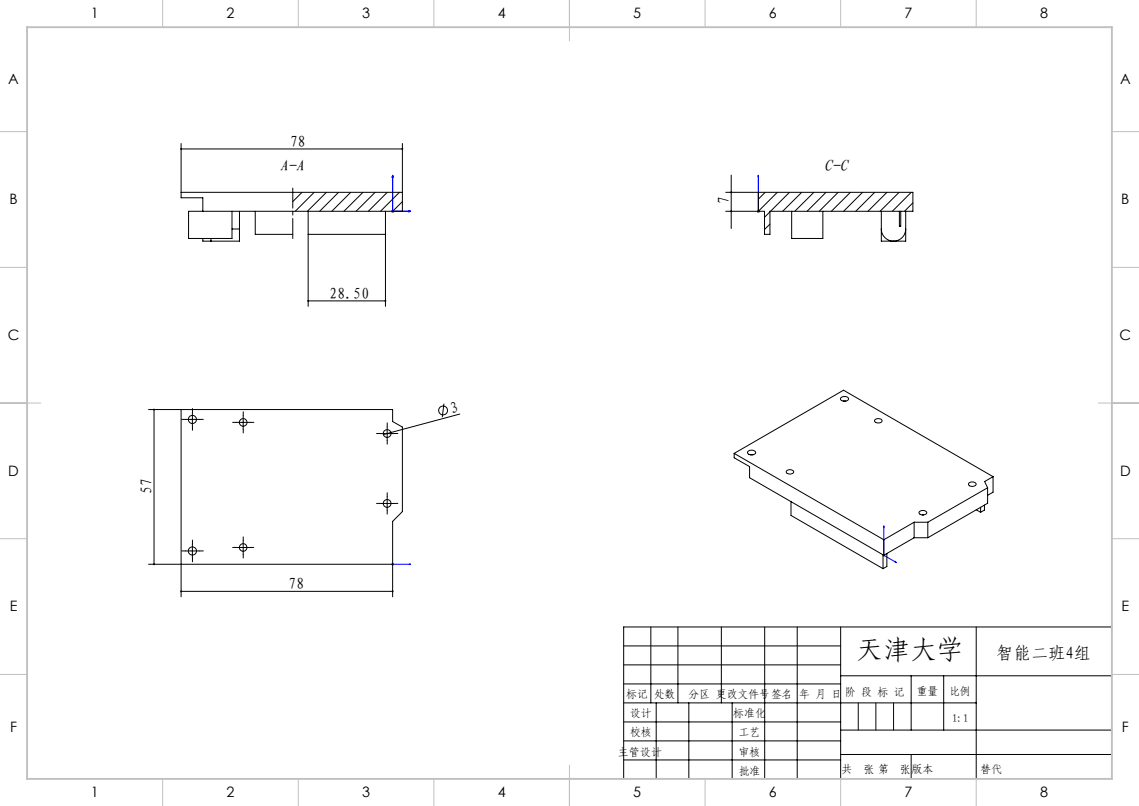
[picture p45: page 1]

天津大学 | 智能二班4组

标记 | 处数 | 分区 更改文件号签名 | | 年 月 日
设计 | | | 标准化 | | 1:1
校核 | | | 工艺

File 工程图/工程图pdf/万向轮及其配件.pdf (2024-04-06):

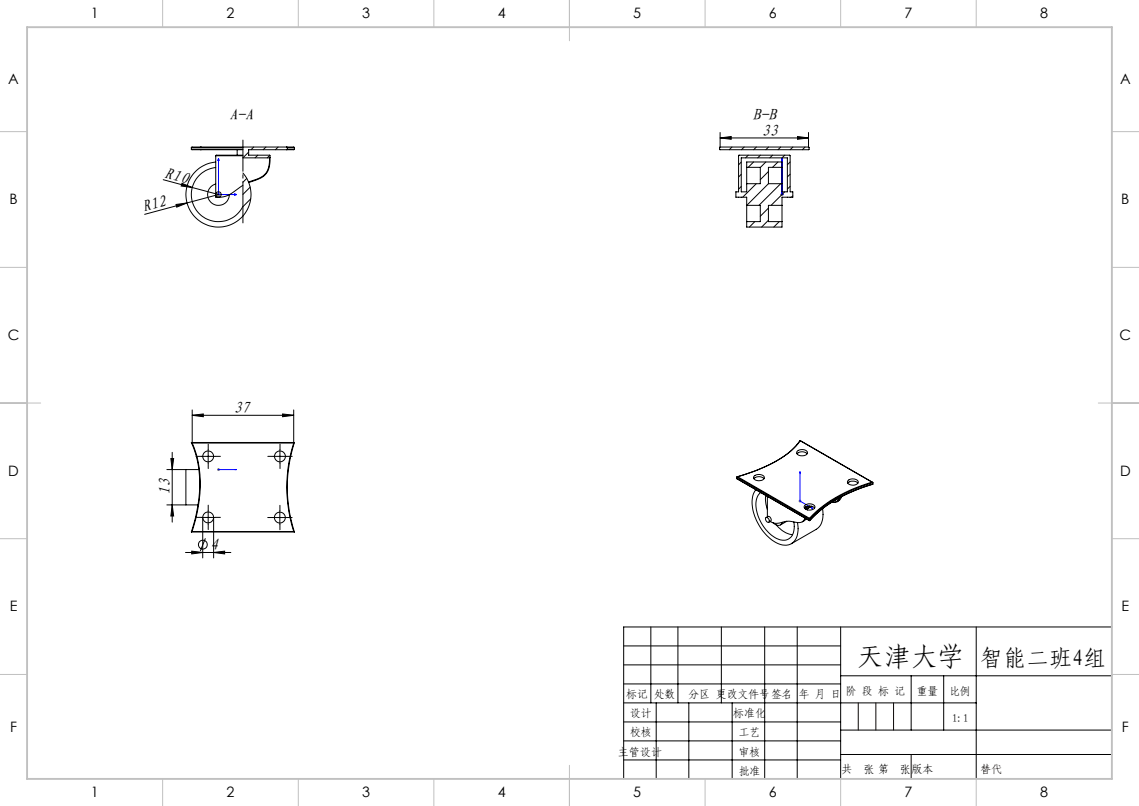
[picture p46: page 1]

天津大学 | 智能二班4组

标记 | 处数 | 分区 更改文件号签名 | | 年 月 日
设计 | | | 标准化 | | 1:1
校核 | | | 工艺

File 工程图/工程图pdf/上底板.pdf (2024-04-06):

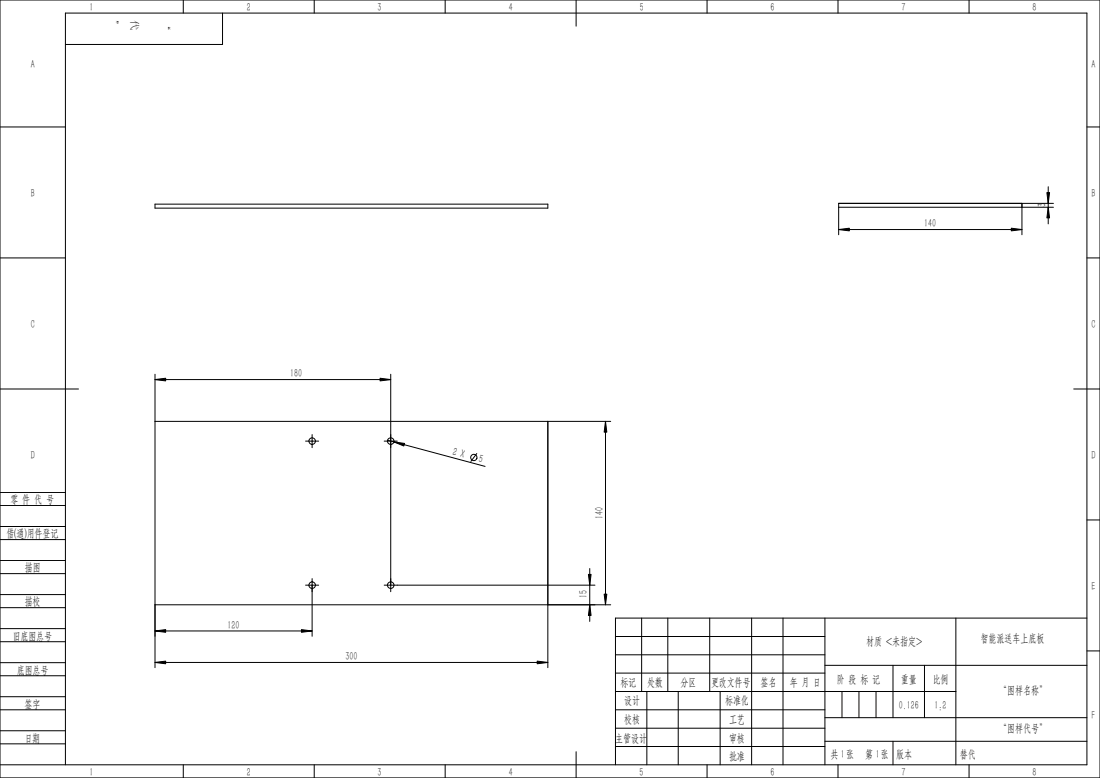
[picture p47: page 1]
底图总号; 旧底图总号; 借(通)用件登记

材质 <未指定> | 智能派送车上底板

阶 段 标 记 | 重量 | 比例 | “图样名称”

标记 | 处数 | 分区 | 更改文件号 | 签名 | 年 月 日
设计 | | | 标准化 | | | | | 0.126 1:2
校核 | | | 工艺
主管设计 | | | 审核

“图样代号”

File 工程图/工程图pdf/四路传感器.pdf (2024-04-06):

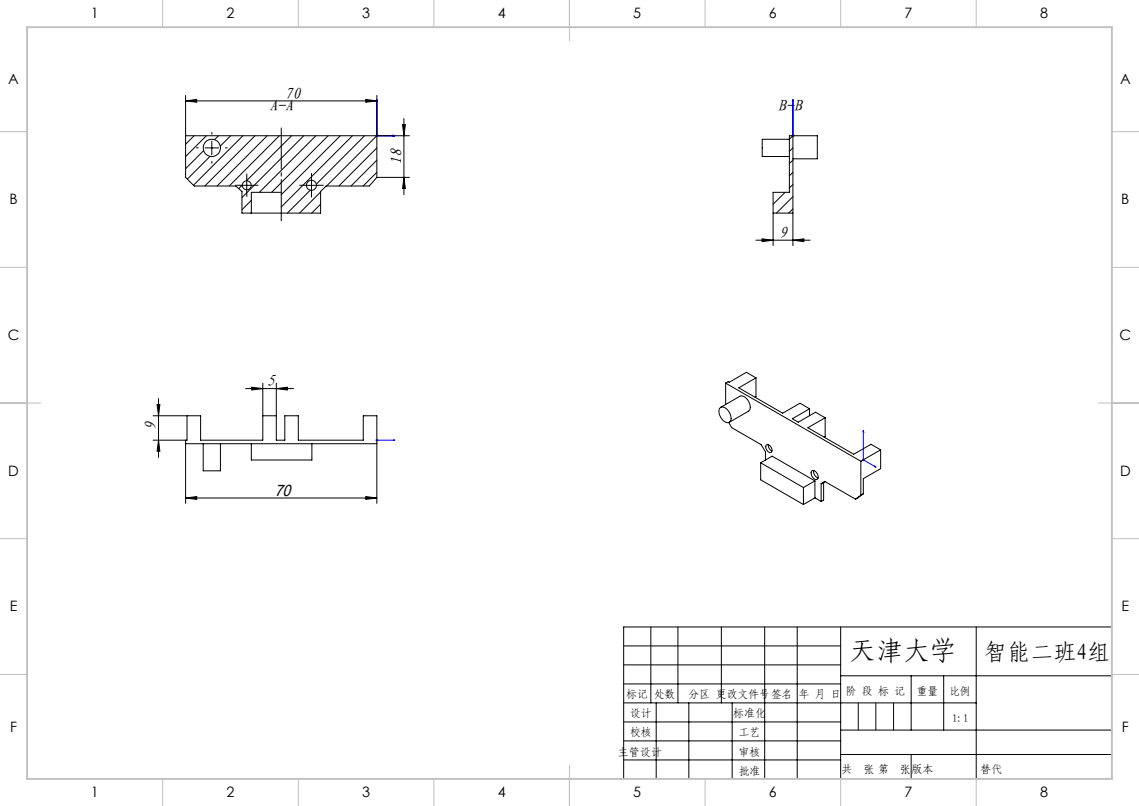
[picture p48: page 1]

天津大学 | 智能二班4组

标记 | 处数 | 分区 更改文件号签名 | | 年 月 日
设计 | | | 标准化 | | 1:1
校核 | | | 工艺

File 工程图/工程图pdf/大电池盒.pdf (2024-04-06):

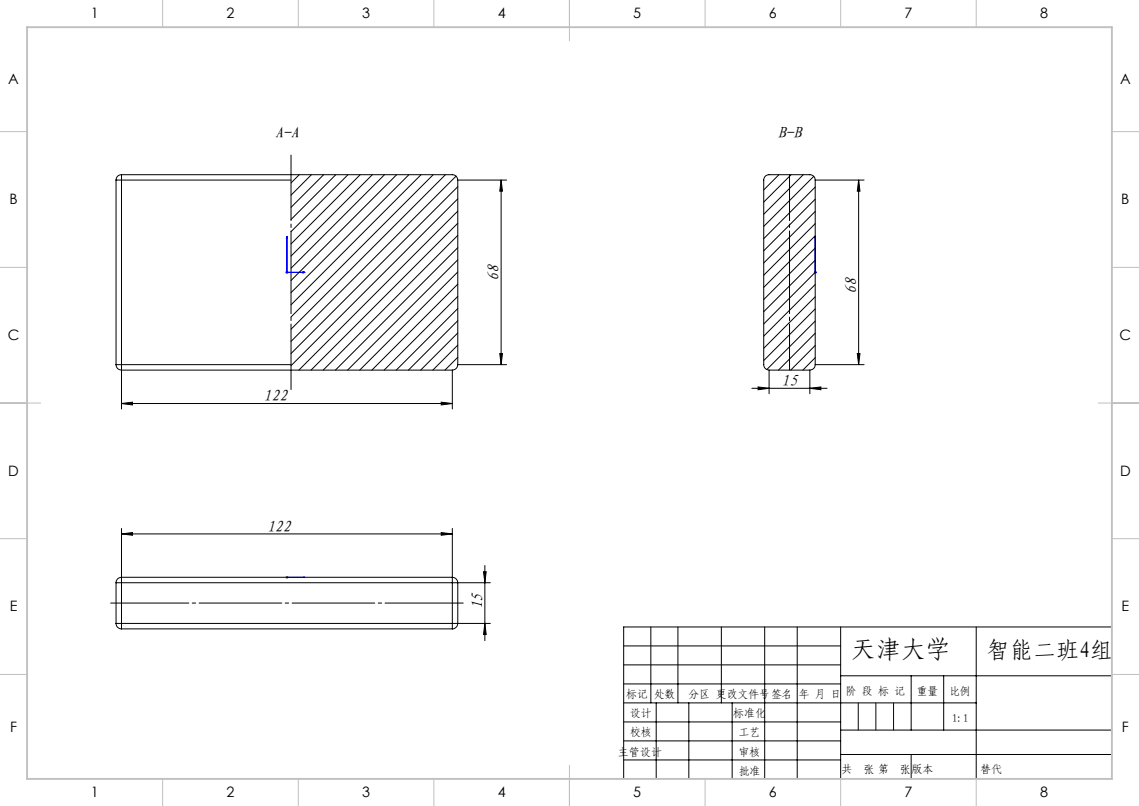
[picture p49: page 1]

天津大学 | 智能二班4组

标记 | 处数 | 分区 更改文件号签名 | | 年 月 日
设计 | | | 标准化 | | 1:1
校核 | | | 工艺

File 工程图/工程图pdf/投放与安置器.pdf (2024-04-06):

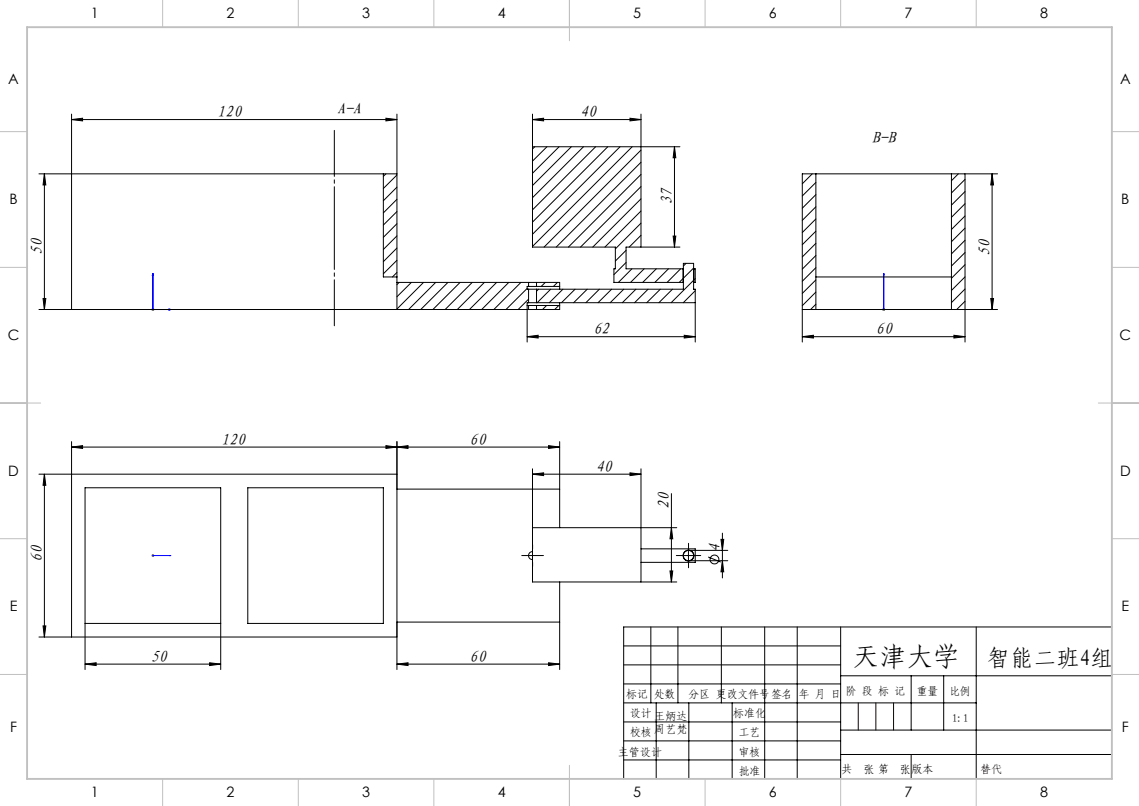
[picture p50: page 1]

标记 | 处数 | 分区 更改文件号签名 | | 年 月 日
设计 王炳达 | | | 标准化 | | 1:1
周艺梵 校核 | | | 工艺

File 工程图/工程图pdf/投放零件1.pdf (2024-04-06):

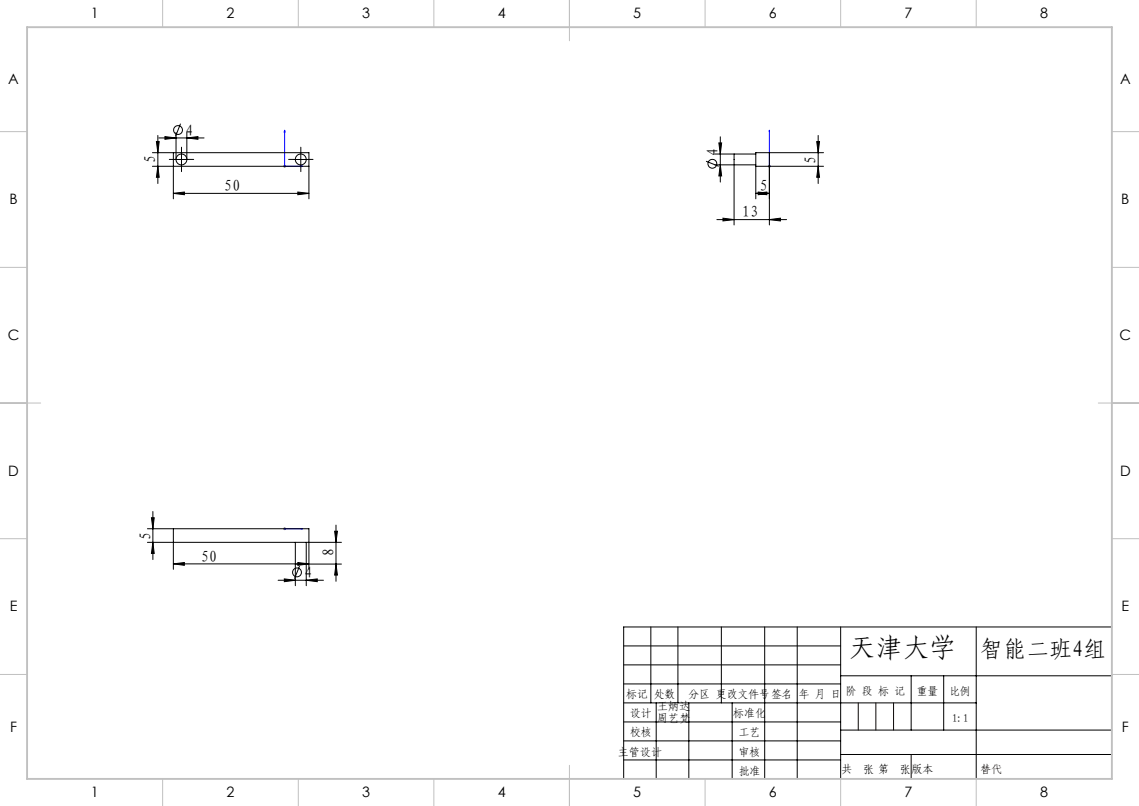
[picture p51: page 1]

天津大学 | 智能二班4组

标记 | 处数 | 分区 更改文件号签名 | | 年 月 日
设计 | 王炳达 周艺梵 | | 标准化 | | 1:1

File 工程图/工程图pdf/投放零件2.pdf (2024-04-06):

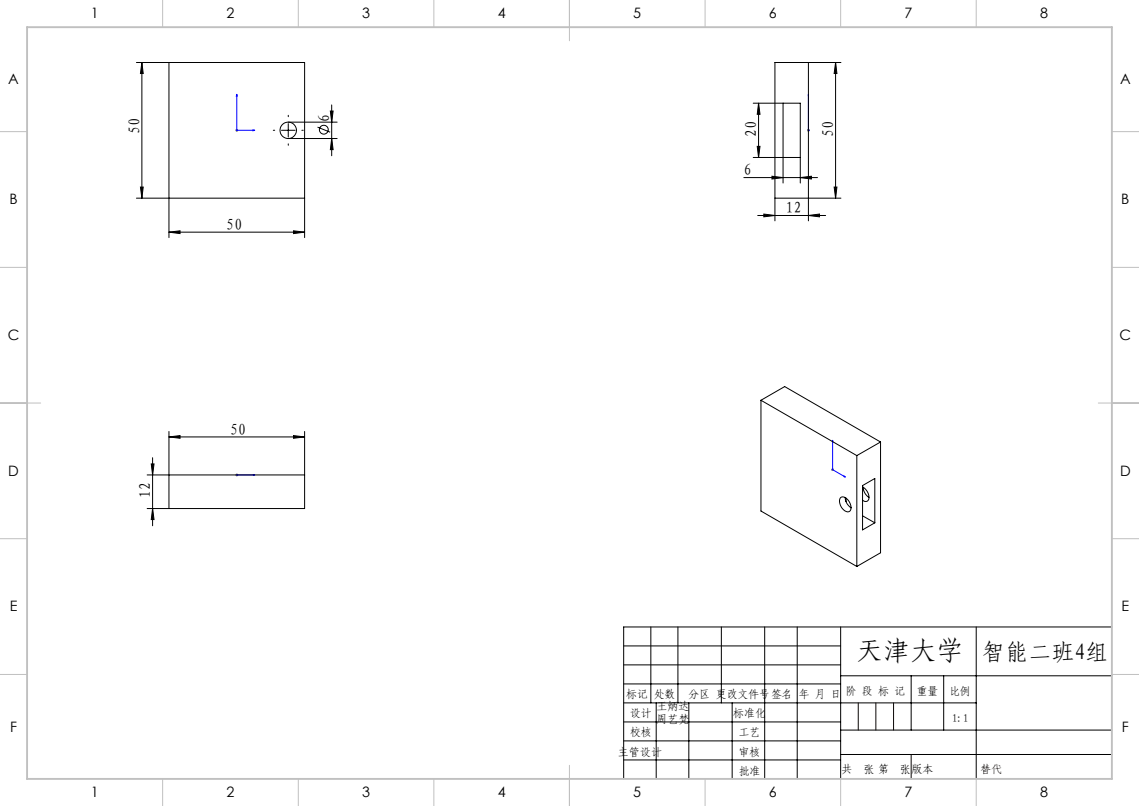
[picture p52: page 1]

天津大学 | 智能二班4组

标记 | 处数 | 分区 更改文件号签名 | | 年 月 日
设计 | 王炳达 周艺梵 | | 标准化 | | 1:1

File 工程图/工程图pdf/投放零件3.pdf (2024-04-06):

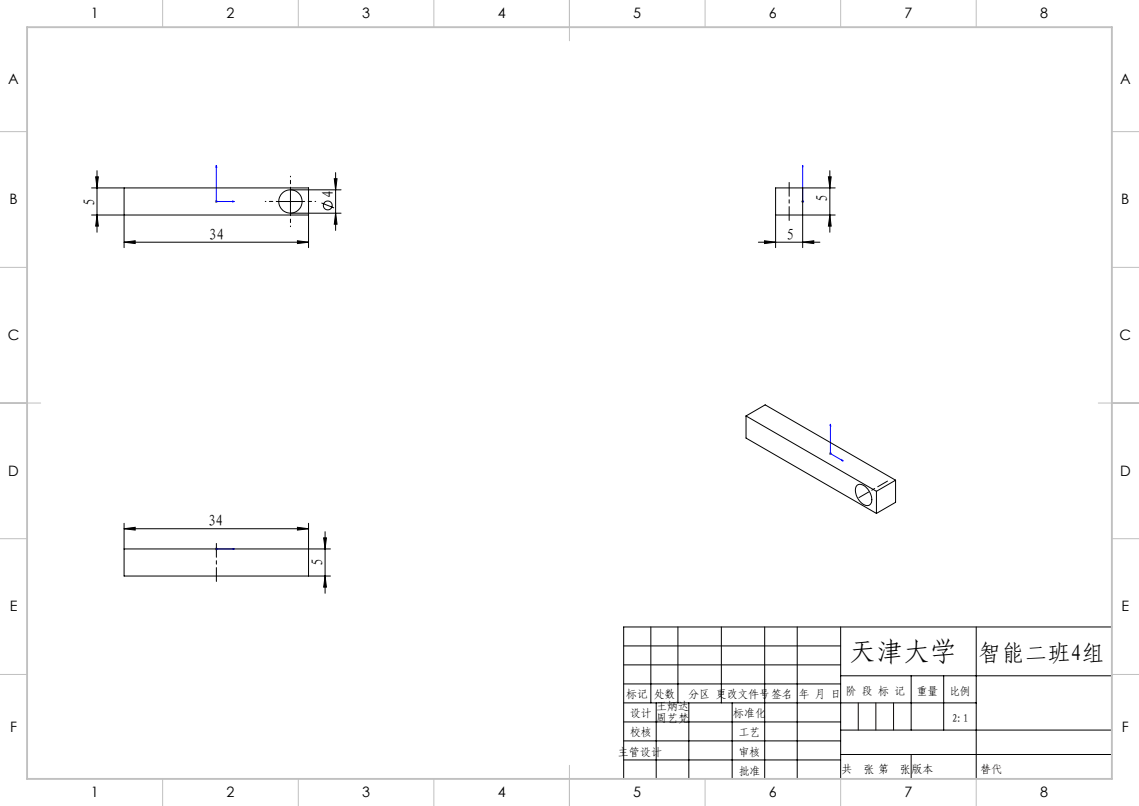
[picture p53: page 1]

天津大学 | 智能二班4组

标记 | 处数 | 分区 更改文件号签名 | | 年 月 日
设计 | 王炳达 周艺梵 | | 标准化 | | 2:1

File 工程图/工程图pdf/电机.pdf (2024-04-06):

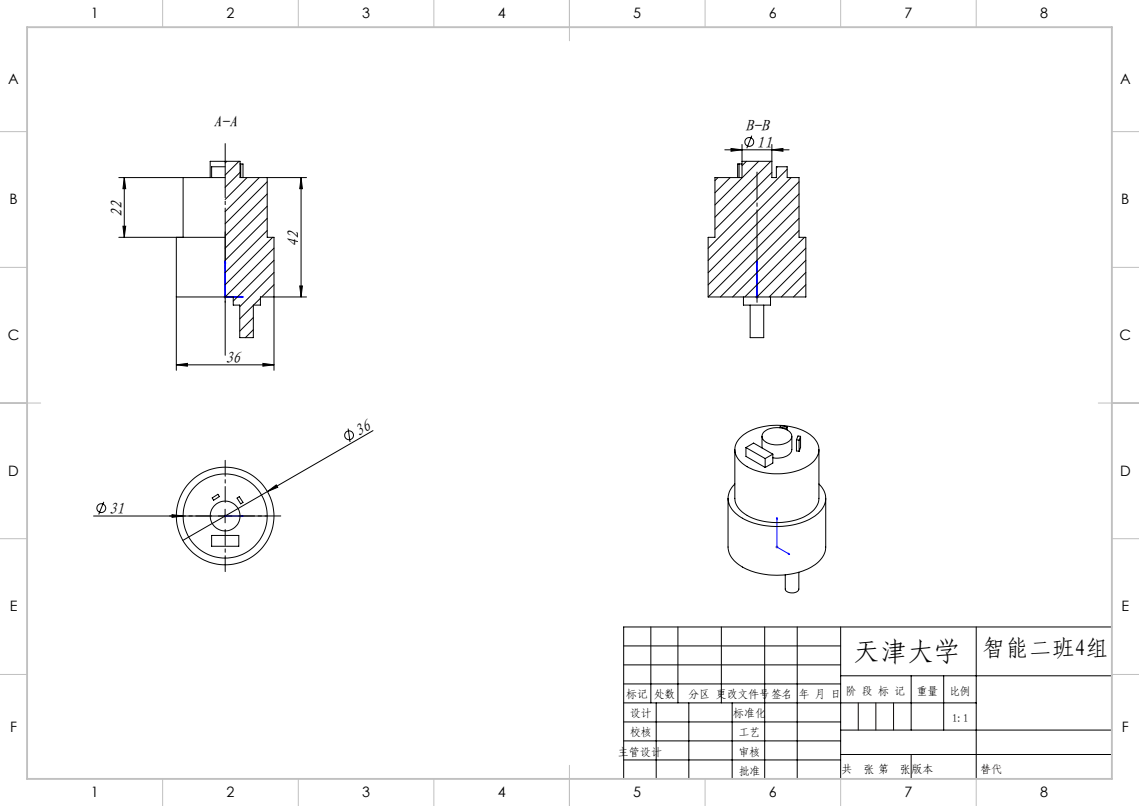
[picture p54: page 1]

天津大学 | 智能二班4组

标记 | 处数 | 分区 更改文件号签名 | | 年 月 日
设计 | | | 标准化 | | 1:1
校核 | | | 工艺
